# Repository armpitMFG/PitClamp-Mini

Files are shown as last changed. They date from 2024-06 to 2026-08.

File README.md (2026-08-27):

# PitClamp Mini
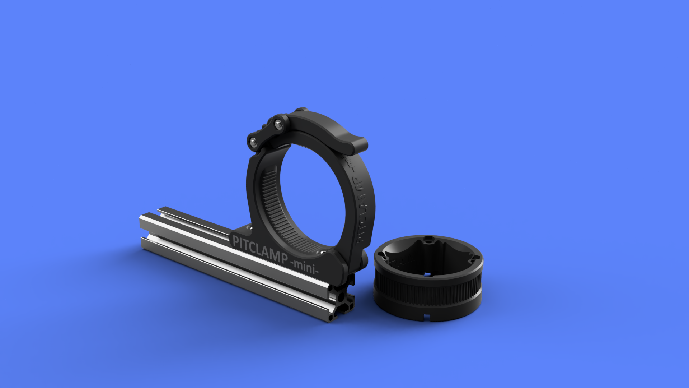
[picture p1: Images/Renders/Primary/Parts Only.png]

## Summary    
3d printed modular quick-release adjustable and removable mount ecosystem for iHSV57, 57AIM, 42AIM, NEMA23 motors. Intended for use with [OSSM](https://www.researchanddesire.com/open-source-sex-machine). 4040/3030 extrusion, flat mount, or clamping base.  

Stress tested to 50 ft-lb without grip being compromised. (PLA 5 walls 15% crosshatch infill)  

### Motor Head Support
  - Default OSSM (57AIM and iHSV57 NEMA23)
  - SpockAroundTheClock's Compact Motor Head (42AIM)
  - just_b's Universal Motor Head (57AIM, 42AIM, and iHSV57 NEMA23)  

### [Purchase A Kit From armpitMFG](https://armpitmfg.etsy.com)

### [Print Files And Instructions](/Files/)  

### [Bill Of Materials](BOM.md)  

### [Assembly Guide Videos](ASSEMBLY_GUIDES.md)

### [Demonstration Videos (SFW)](DEMONSTRATION_VIDEOS.md)

### [Updates](UPDATES.md) (Last updated - 11.22.2024)

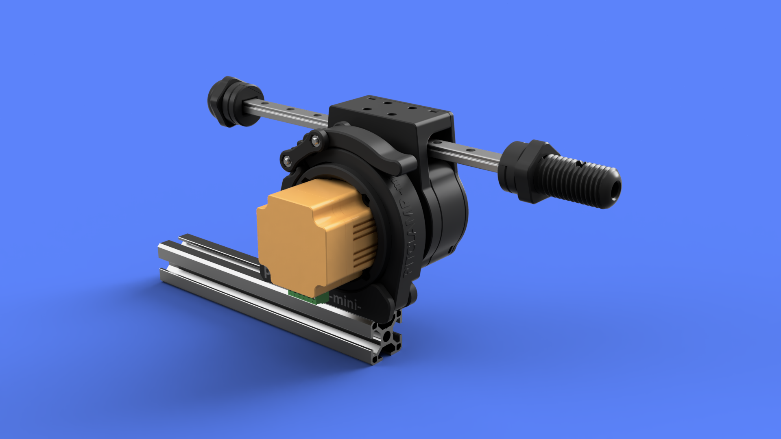
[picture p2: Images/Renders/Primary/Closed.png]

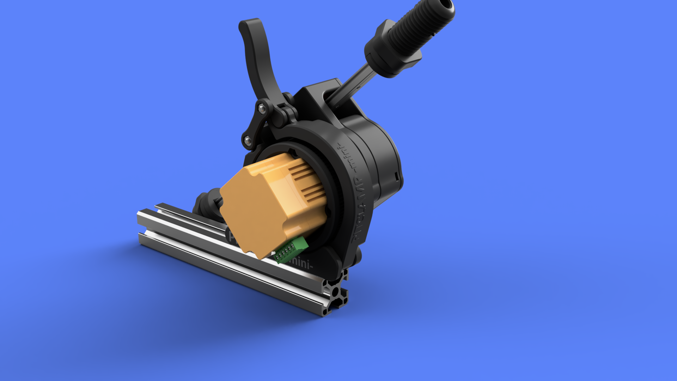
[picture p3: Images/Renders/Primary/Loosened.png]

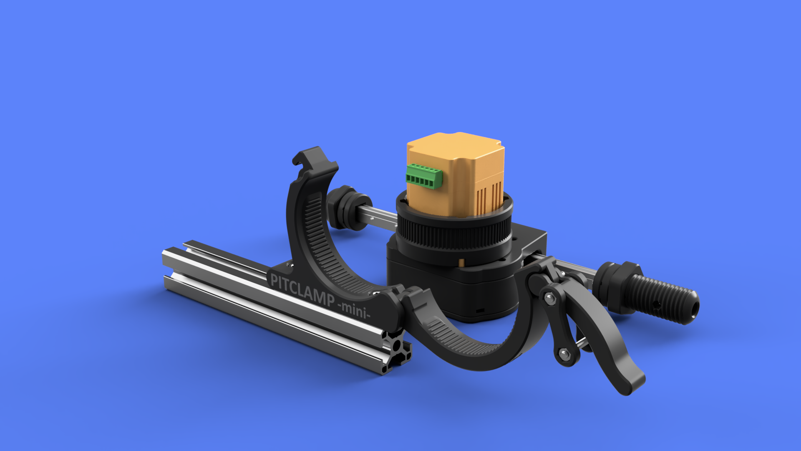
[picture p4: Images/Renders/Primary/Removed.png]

<!-- ![](Images/Renders/View%203/PitClamp%20Mini%20-%2057AIM%20-%20Clamp%20Only.png) -->
<!-- ![](Images/Renders/View%203/PitClamp%20Mini%20-%2057AIM%20-%20Complete.png) -->
<!-- ![](Images/Renders/View%201/PitClamp%20Mini%20-%2057AIM%20-%20Fully%20Open.png) -->
<!-- ![](Images/Renders/View%201/PitClamp%20Mini%20-%2042AIM%20-%20Complete.png) -->

## Features  
  - 4 degree precision quick-adjustable rotation
  - Motor can be quickly removed from mount for storage or use in another base
  - Selection of bases for different use cases
    - Extrusion Top Mount
      - (Extrusion agnostic, but was designed for as small as 3030)
    - Quick Clamp Ratchet + 3030 Extrusion Mount
      - (This mount is the reason behind the whole project)
      - POWERTEC 71408 is the clamp pictured
      - "Guide rail MFT ratchet clamp" search term to find similar prodcuts
    - Double Hinge Folding Mount
       - (Folds flat for easier frame storage, e.g. sliding under bed)
    - (FUTURE) Fully printed Tabletop Clamp
    - (FUTURE) PitClamp-As-Hinges
    - (FUTURE) Pneumatic SC40 Cylinder Pump
  - (FUTURE) Relocatable OSSM Reference Board v2
  - (FUTURE) (Optional) Capacitor located on motor for solder-less pre-v2.3 board compatability  

## Motor Rings

**57AIM - 57AIM15, 57AIM30**  
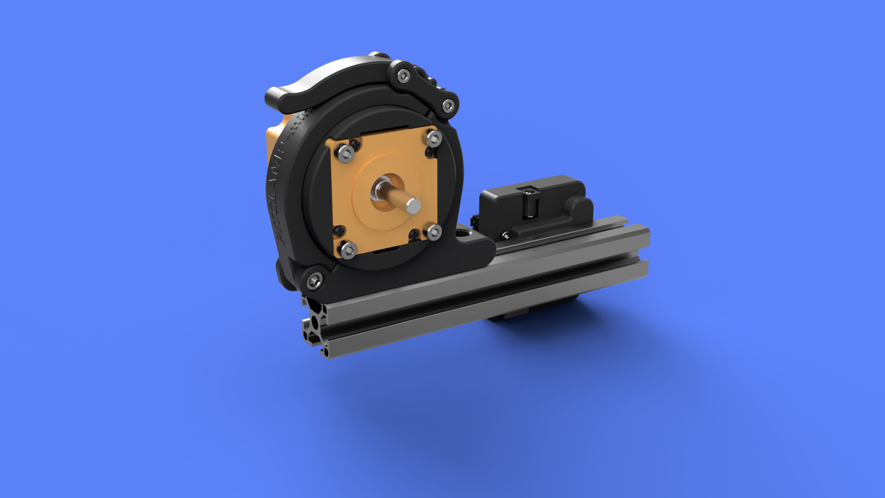
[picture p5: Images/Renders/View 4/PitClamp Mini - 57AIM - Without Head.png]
  
<!-- ![](Images/Renders/View%201/PitClamp%20Mini%20-%2057AIM%20-%20Complete.png)   -->
**iHSV57 -  100w, 140w, 180w**  
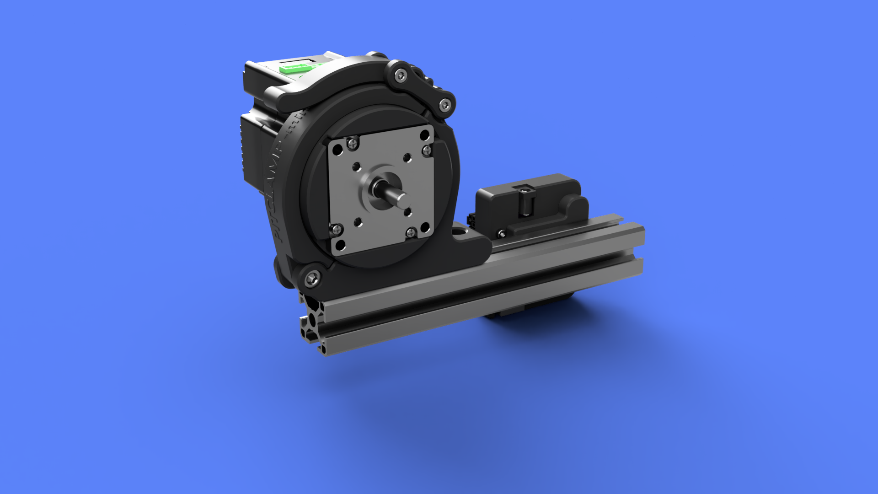
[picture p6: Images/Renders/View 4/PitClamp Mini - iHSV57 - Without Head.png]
  
<!-- ![](Images/Renders/View%201/PitClamp%20Mini%20-%20iHSV57%20-%20Complete.png)   -->
**42AIM - 42AIM15, 42AIM30**
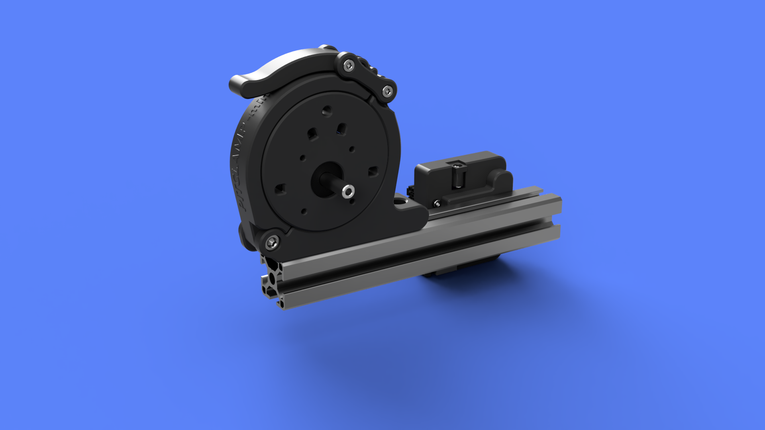
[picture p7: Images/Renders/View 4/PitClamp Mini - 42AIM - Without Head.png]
  
<!-- ![](Images/Renders/View%201/PitClamp%20Mini%20-%2042AIM%20-%20Complete.png)   -->

## Photos
<!-- ![](Images/Photos/PitClamp%20Mini%2057AIM30%204040%20Extrusion.jpg)  
![](Images/Photos/PitClamp%20Mini%2057AIM30%204040%20Extrusion%20Front.jpg)  -->
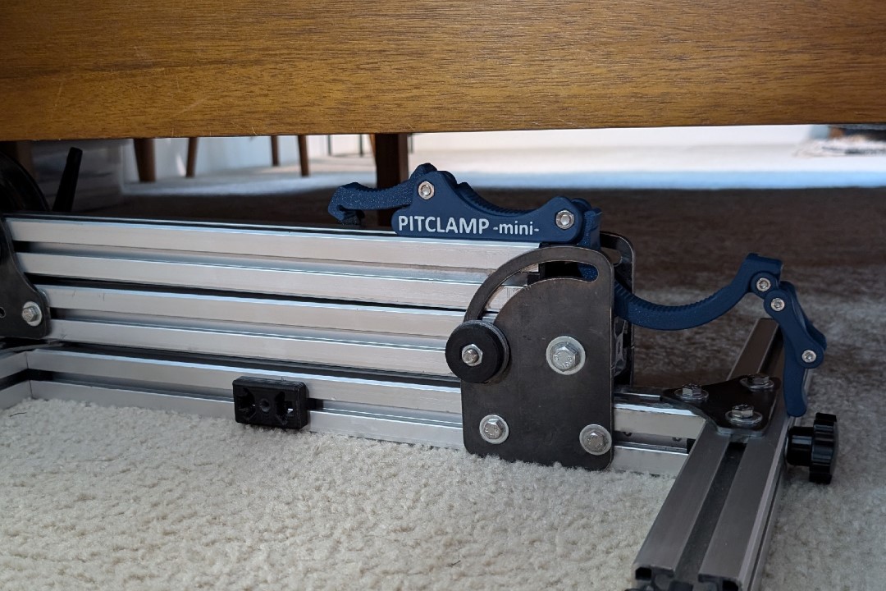
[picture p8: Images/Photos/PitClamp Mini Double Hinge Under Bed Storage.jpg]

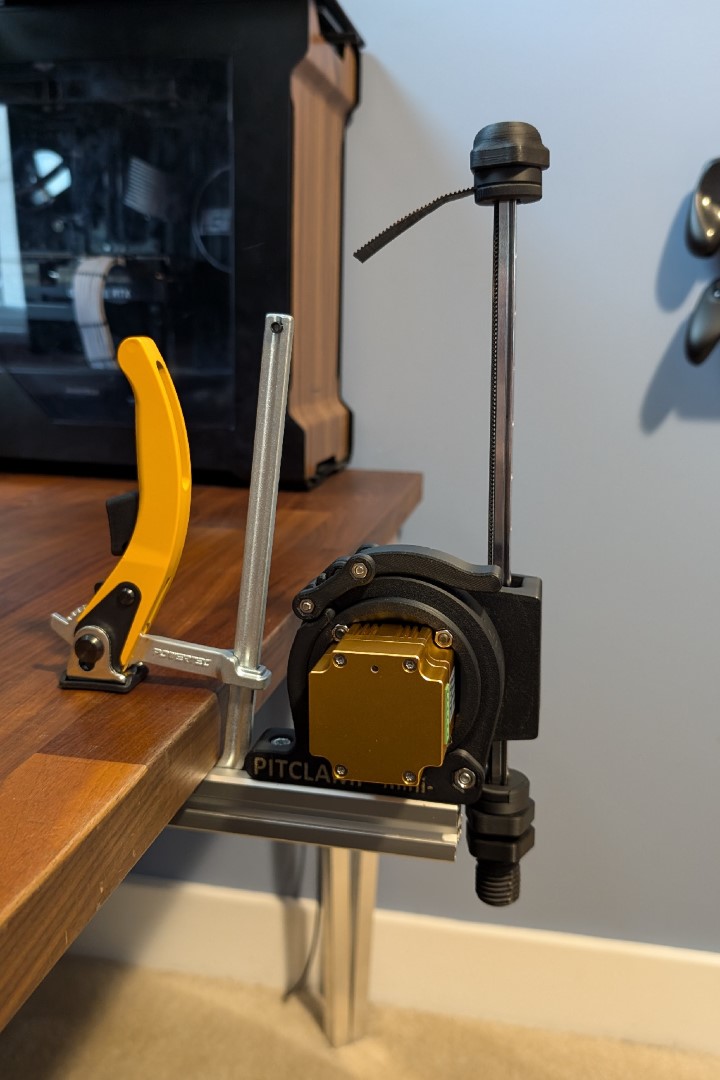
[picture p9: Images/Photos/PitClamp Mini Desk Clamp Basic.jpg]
  
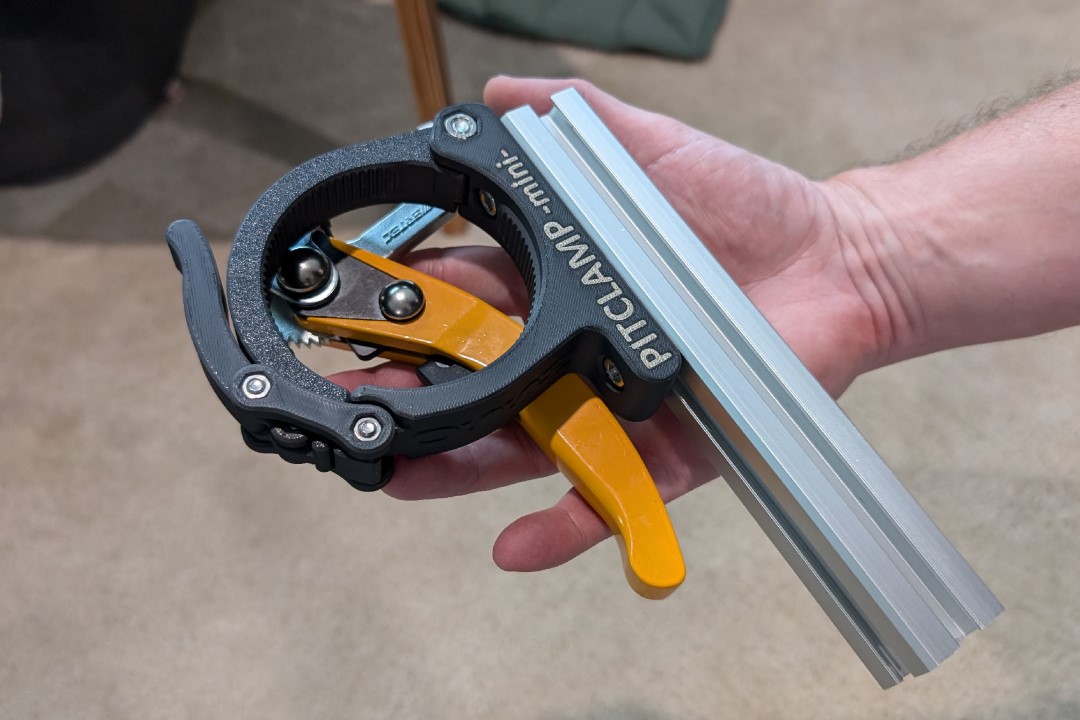
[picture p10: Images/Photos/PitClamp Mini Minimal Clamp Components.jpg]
  
<!-- ![](Images/Photos/PitClamp%20Mini%2057AIM30%203030%20Extrusion%20Modular.jpg) -->
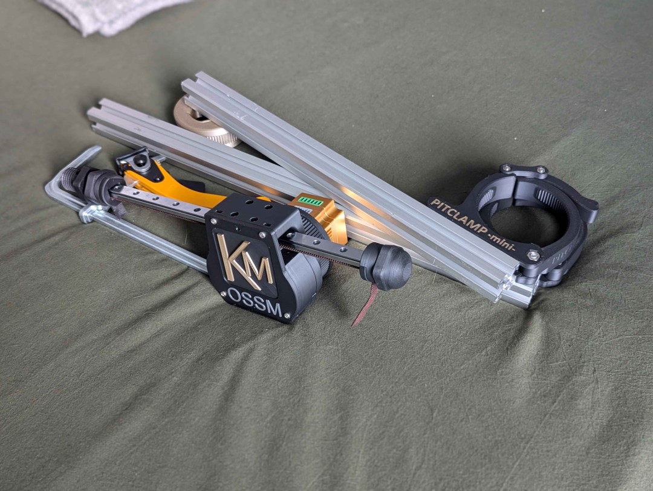
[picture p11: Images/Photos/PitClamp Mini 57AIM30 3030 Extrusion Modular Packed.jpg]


## Roadmap  
**Motor Rings:**
  - 42AIM Motor Ring: 100%  
  - 57AIM Motor Ring: 100%
  - iHSV57 Motor Ring: 100%
  - Extrusion Adapter Ring: 100%

**Clamping Components:**
  - Upper Clamp: 100%  
  - Handle: 100%  
  - Dogbones: 100% 
  - 4040/3030 Extrusion Base: 100%
  - Double Hinge Folding Base: 100%
  - Quick Clamp Tabletop Base: 100%
  - 3d Printed Tabletop Base: 20%
  - (Experimental) Side Mounted PitClamp Mini Hinge Pair: 80%
  - Pneumatic SC40 Cylinder Pump Base: 20%

**Relocatable Reference Board:**
  - Reference Board Case: 75%  
  - Reference Board 4040 Bracket: 90%
  - 42AIM Motor Plug Tidy w/ Capacitor: 75%
  - 57AIM Motor Plug Tidy w/o Capacitor: 0%

**Rail Components:**
  - Screwcap Mini Tensioner: 100%
  - Mini End Effector: 100%
  - XL End Effector: 100%

## Changes from PitClamp v3 
  - Support added for 42AIM motor  
  - Motor ring diameter reduced by 15%  
  - Overall filament required reduced by over 25%  
  - Clamp rotational grip strength increased
  - Motor ring is now reversible in the mount  
  - Clamp "helper" added to reduce adjustment noise/clunkyness  
  - Rear hinge pin is no longer a printed piece
  - Print clarity improved (and optional-default-none) for first and last layer "PitClamp Mini" & "armpitMFG" branding  

## Legacy PitClamp Bases
These bases are being reworked for the PitClamp Mini form factor

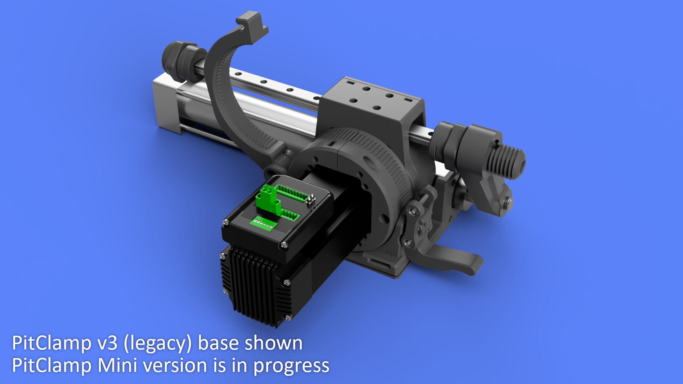
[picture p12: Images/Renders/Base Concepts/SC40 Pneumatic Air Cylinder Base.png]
  
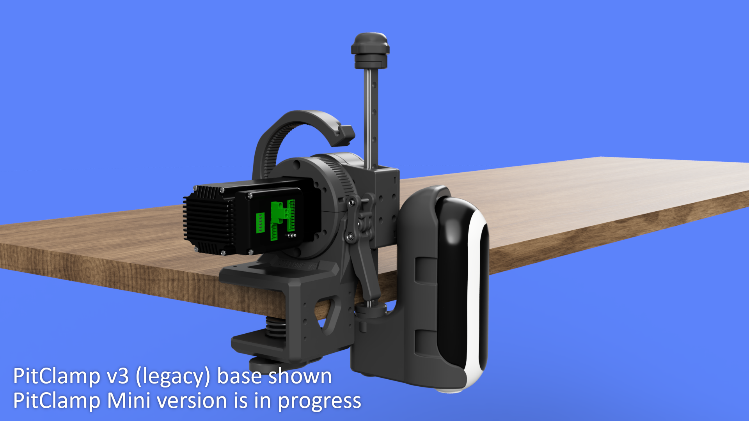
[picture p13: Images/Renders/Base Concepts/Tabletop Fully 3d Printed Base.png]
  

## Licensing

Open-source hardware under the
**[CERN Open Hardware Licence Version 2 - Strongly Reciprocal](LICENSE)**
(`CERN-OHL-S-2.0`), the same licence as the
[OSSM project](https://github.com/KinkyMakers/OSSM-hardware).

Copyright and attribution: [NOTICE.md](NOTICE.md).

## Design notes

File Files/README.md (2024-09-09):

Check out the [Preconfigured 3mf Files](Preconfigured%203mf%20Files/) directory for slicer files that contain all required parts with support and other print settings preconfigured. Just delete the rings that don't apply to your build, select your filament and send the job to your printer. EZ

## Printing:
The entire project is intended for:  
  - 0.4mm nozzle (Wider should not cause problems)
  - 0.2mm layer height (Necessary for some built-in helper features)
  - Standard strength (5 wall) profile
  - 15% gyroid or crosshatch infill
    - Higher infill optional

All parts tested in PLA and PETG  

Supports required for:
  - PitClamp Mini - Common - Handle
  - PitClamp Mini - Base - Standard - Lower
  - PitClamp Mini - Common - Upper
  - PitClamp Mini - Ring - 57AIM
  - PitClamp Mini - Ring - iHSV57

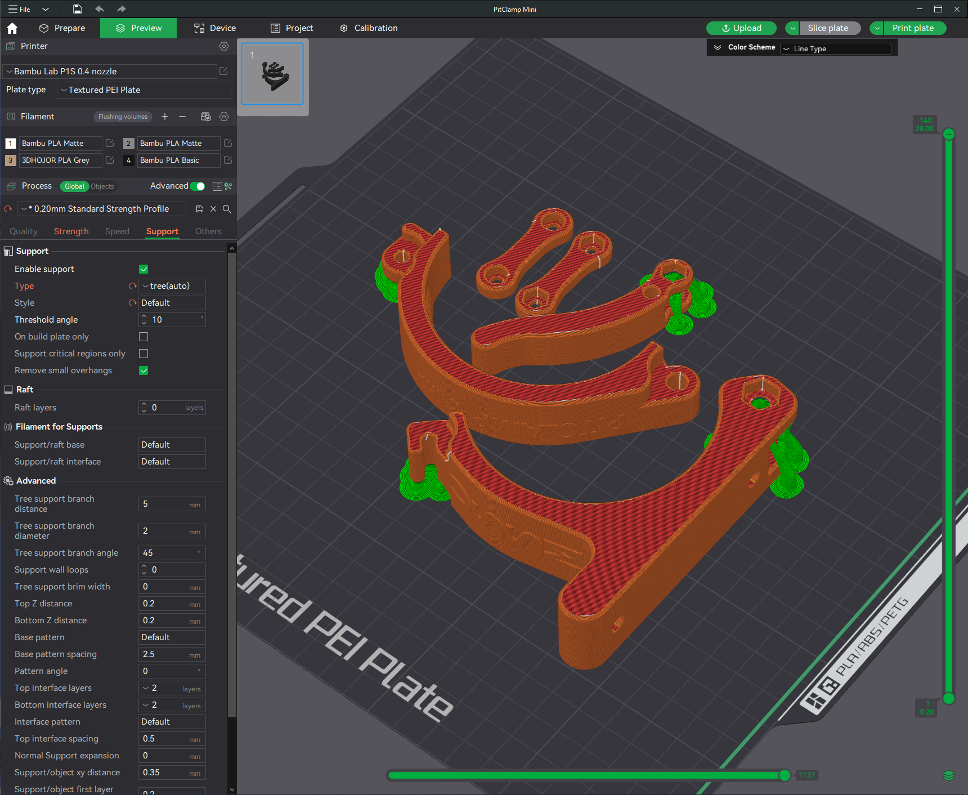
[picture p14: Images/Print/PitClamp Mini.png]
  
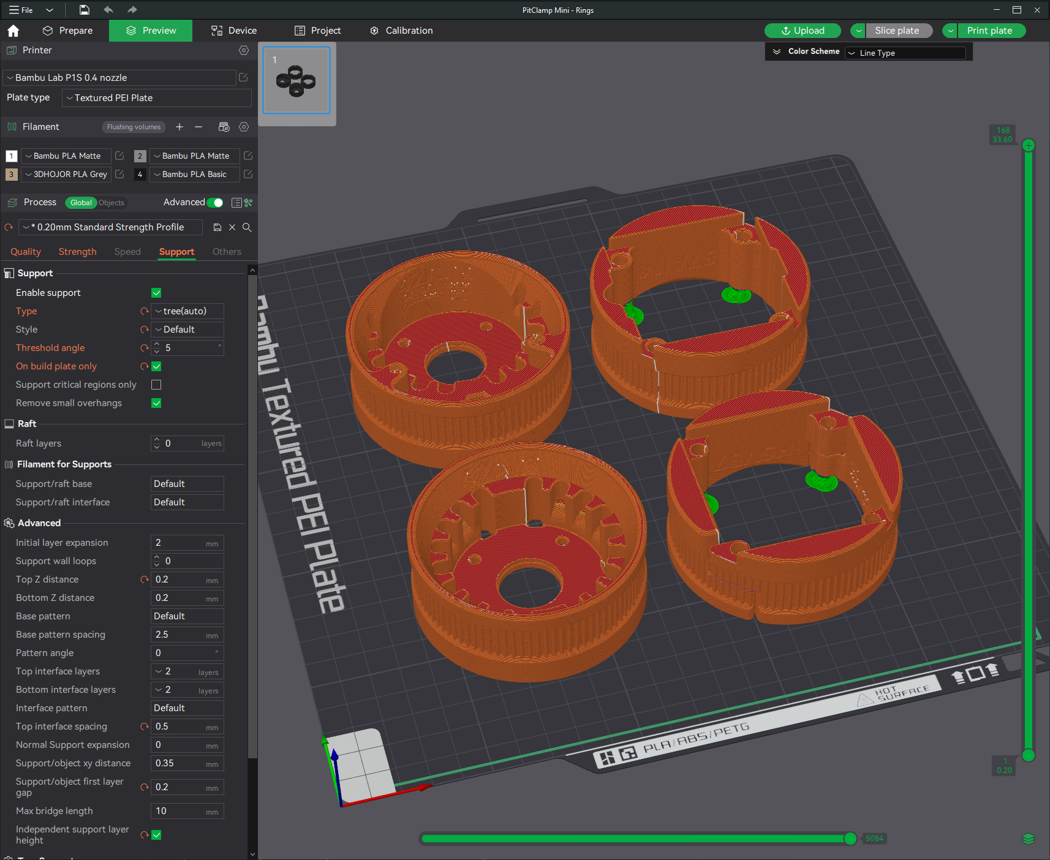
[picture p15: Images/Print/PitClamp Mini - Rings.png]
  

Optional accent color for logo.  
Requires AMS, just paint bucket the flush lettering faces:
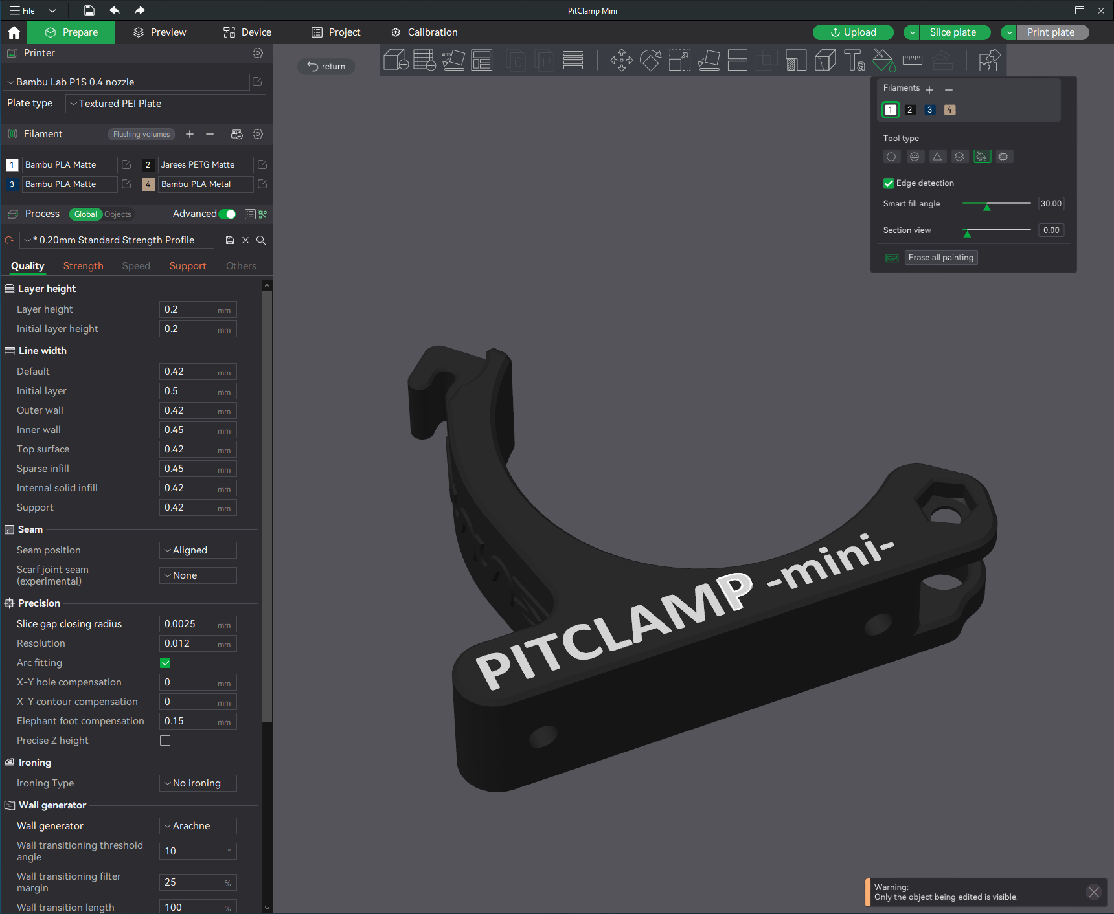
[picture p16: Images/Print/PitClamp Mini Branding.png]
  

## Rings
### Ring Offsets:
- **5mm/6mm offsets** provide clearance for 4040 extrusion. Fine for 3030 setups as well.
    - These are the recommended ring offsets for all setups.
- **0mm/1mm offsets** are designed to sit close to 3030 extrusion. 
    - Only use this offset if you _really_ need things to be compact on 3030 setups. Can have clearance issues if your setup isn't absolutely perfect.

### 42AIM
    For 42AIM motors

### 57AIM
    For 57AIM "Gold" motors

### iHSV57
    For iHSV57 motors.  
    
    This ring is two parts but by using some design trickery it prints as one with minimal supports.  
    
    Ring snaps into two pieces after removing from printer.  
    
    Clasp each half around the motor.

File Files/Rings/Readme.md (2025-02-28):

    //TODO Fill this out better.  

v1.1 Ring (only available for 57AIM) can use M5 nuts or M5 Coupling Nuts (20mm) and has ridges for an interlocking connection to an optional rear motor cover. This is the recommended setup.  
This ring uses 4x M5x35 to attach to the OSSM motor head.

### Pick a ring for your motor based on which actuator head design you are using.  
 - **"Default"** has two diagonal motor mounting bolts recessed an additional 5mm.
    - This is to match the Default OSSM motor head allowing for 4x m5x40mm to be used instead of needing m5x45 for two of them due to the offsets of these mounts in the motor head.
 - **"Alternate"** has all 4 motor mounting bolts recessed the same amount.
    - This is for motor heads such as "Universal motor head" which have matching bolt lengths for assembly.

After testing various designs, the offset has been standardized at +5mm to allow ample clearance for rail tensioners and a sturdier ring.  

Passthru allows for the option of running wires through the ring.  

Most common would be 57AIM - Default, which uses ["PitClamp Mini - Ring v1.1 - 57AIM - 5mm Offset +Passthru.stl"](https://github.com/armpitMFG/PitClamp-Mini/blob/main/Files/Rings/PitClamp%20Mini%20-%20Ring%20v1.1%20-%2057AIM%20-%205mm%20Offset%20%2BPassthru.stl)

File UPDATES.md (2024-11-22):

A stream of updates made to this repo

_Links may go bad, if a reference changes I am not keeping it updated in this file._

- 11.22.2024 - Added v1.1 57AIM Ring (Latest recommended default)
- 09.08.2024 - Refactored file structure.
- 09.08.2024 - Updated to new default files to simplify BOM. 
- 09.04.2024 - Added **Standard Base w/ Helper Brim** STEP file to [Files](/Files/) folder _(Helps prevent latch corner from lifting during print)_
- 09.03.2024 - Added **Ring Template** STEP files to [Ring Template](/Files/Ring%20Template/) folder
- 09.03.2024 - Added **Centered 42AIM Ring** to [Non-Standard Parts](/Files/Non-Standard%20Parts/) folder _(Compatibility with just_b's motor head)_
- 08.29.2024 - Added **57AIM Cable Passthru** Ring to [Non-Standard Parts](/Files/Non-Standard%20Parts/) folder _(Experimenting with motor head mounted Reference Board)_
- 08.28.2024 - Added **[Print-In-Place PitClamp Mini](/Files/Experimental/Print%20In%20Place/)** to [Experimental Parts](/Files/Experimental/) folder _(Reduced hardware)_
- 08.28.2024 - Revised **Extrusion Ring** from Normal to Experimental status _(Needs a stronger design for re-release)_

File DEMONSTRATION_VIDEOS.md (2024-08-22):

##   Modular Mount Demonstration  
[PitClamp Mini - Modular Mount Demonstration  
https://www.youtube.com/watch?v=qSyPyNlI1cM](https://www.youtube.com/watch?v=qSyPyNlI1cM)  

##   Desk Clamp Demonstration
[PitClamp Mini - Desk Clamp Demonstration  
https://www.youtube.com/watch?v=EhhH3YP36sw](https://www.youtube.com/watch?v=EhhH3YP36sw)  

##   Torque test to failure (OSSM Head Failure)
[PitClamp Mini - Torque test to failure  
https://www.youtube.com/watch?v=X3qTg1i2Ts0](https://www.youtube.com/watch?v=X3qTg1i2Ts0)

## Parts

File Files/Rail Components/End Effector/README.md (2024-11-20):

## Multipurpose End Effector Tensioner

Inspired by Jack's 24mm effector + tensioner  
Inspired by JRG's clampring tidy-up

**Notes**  
Multipurpose_End_Effector_Tensioner_Medium is the end I would recommend.   
Multipurpose_End_Effector_Tensioner_Short will give you 25mm additional travel but should be reserved for non-heavy-duty applications  

**Summary**  
//TODO

**Hardware**  
2x m3x16 + nuts

**Printing**  
Use a 2 layer raft under the threads for better adhesion  
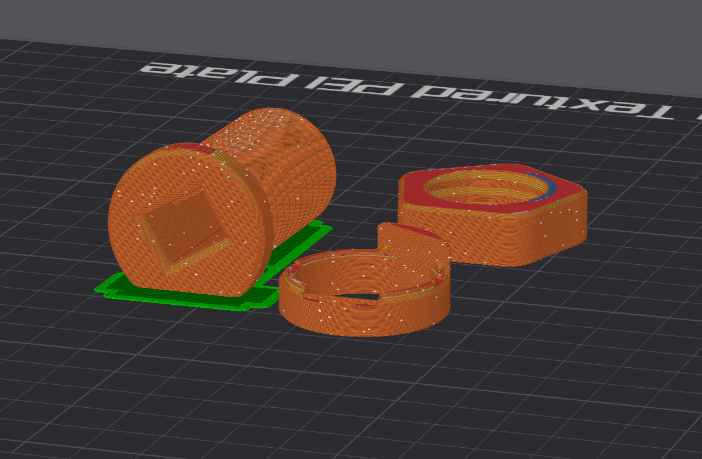
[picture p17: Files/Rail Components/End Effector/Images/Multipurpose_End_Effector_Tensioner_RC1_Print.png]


**Assembly**  
//TODO

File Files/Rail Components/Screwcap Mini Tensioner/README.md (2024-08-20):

## Screwcap Mini Tensioner
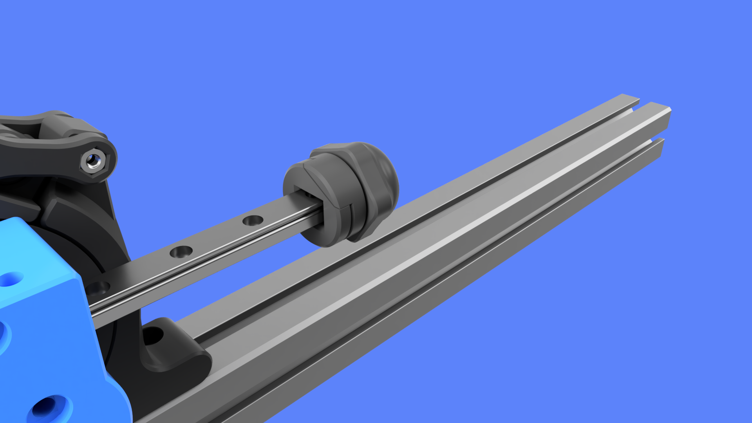
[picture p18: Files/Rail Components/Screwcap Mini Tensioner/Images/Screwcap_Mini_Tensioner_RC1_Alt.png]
Cover Photo


**Summary**  
This is a compact belt tensioner that supports up to 12mm belts.  
Smooth-styling, no exposed hardware. Safer for accidental contact.  

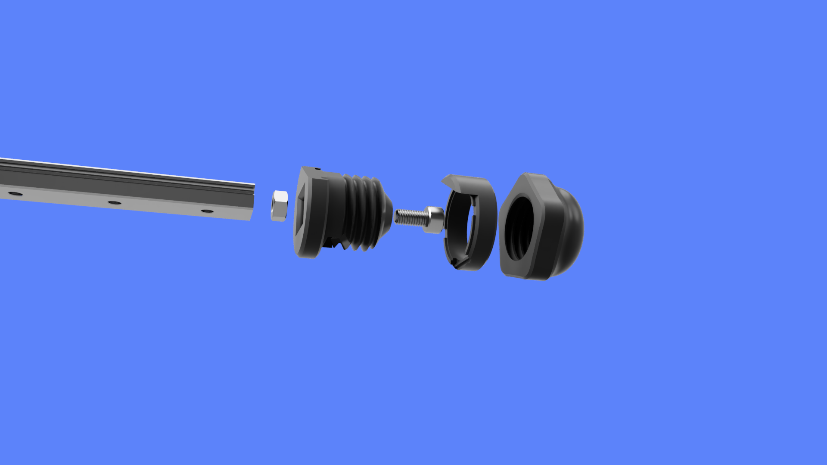
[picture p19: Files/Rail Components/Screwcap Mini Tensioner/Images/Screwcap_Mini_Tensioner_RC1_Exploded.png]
Exploded view

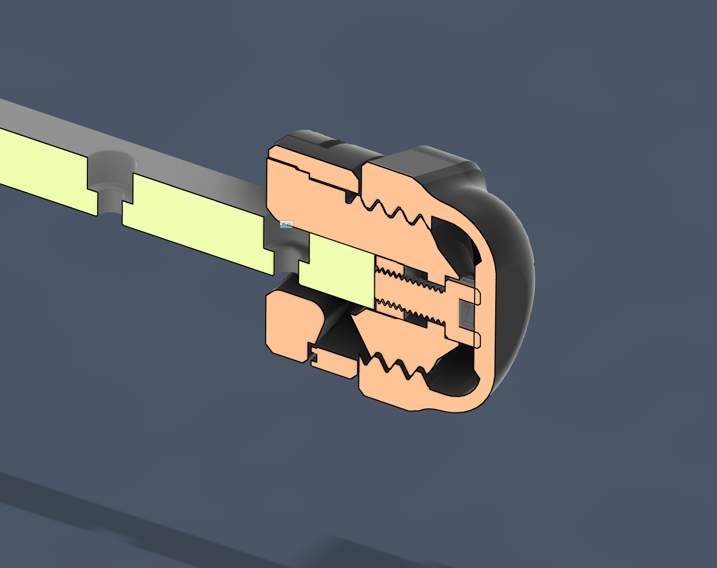
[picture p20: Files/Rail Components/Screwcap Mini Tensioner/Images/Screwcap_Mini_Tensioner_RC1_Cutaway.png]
Cutaway view


**Hardware**  
M5x10 Socket Cap Head Bolt  
M5 Nut

**Printing**  
Recommended profile: Strength, 20% infill

Screwcap_Mini_Tensioner_Ring - No supports  
Screwcap_Mini_Tensioner_Cap - Supports necessary, just needs to hold up the middle  
Screwcap_Mini_Tensioner_Base - Print on a small raft, I used 2 layer raft

For best results, print using "Variable layer height" for Screwcap_Mini_Tensioner_Base and Screwcap_Mini_Tensioner_Cap. It's really worth the extra time here.

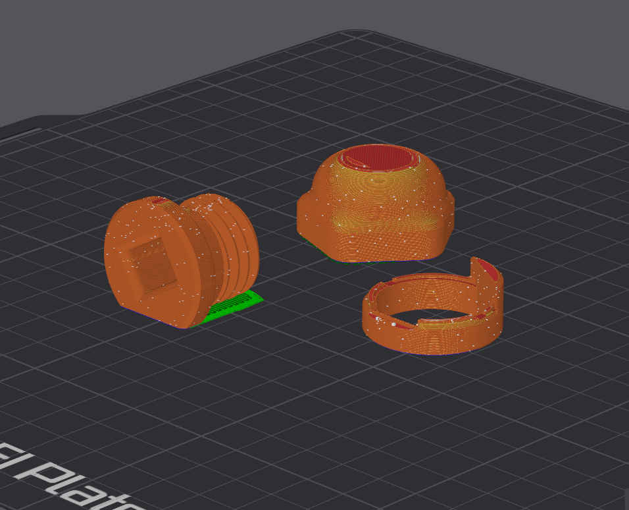
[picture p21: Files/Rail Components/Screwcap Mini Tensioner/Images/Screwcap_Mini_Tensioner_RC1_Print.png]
Print view


##   Screwcap Mini Tensioner Installation

[Screwcap Mini Tensioner Installation  
https://www.youtube.com/watch?v=DaN17W8FflY](https://www.youtube.com/watch?v=DaN17W8FflY)
 
**Assembly**  

Drop nut into the Base. Screw in the bolt lightly from the other side until the nut is secured into the base of the hole.  
Loosen the bolt unil there is small gap visible between it and the Base  
Slide belt through Base opening, slide base onto rail  
Pull tension on the belt while sliding the Ring into place  
While keeping tension on the belt, screw on the cap.

You should feel the cap hit the head of the screw, and as you tighten from there it will move the tensioner away from the rail while also tightening it's grip on the belt. Unscrew and adjust the bolt position and repeat the process if you need to vary the tension.

**Attributions**  
Inspired by Jack's 24mm effector + tensioner  
Inspired by JRG's clampring tidy-up

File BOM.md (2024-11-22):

# PitClamp Mini Bill Of Materials 

## Motor Rings:

### 57AIM 
Default Motor Head, use Default (v1.1 ring)  
Alternate Head, use Alternate

    v1.1 ring - can use 4x M5x35 Socket Cap Head Bolt (Default that are included with R+D OSSM parts kit)
    Other rings - use 4x M5x40 Socket Cap Head Bolt
    4x M5 Nuts

### iHSV57
Default Motor Head, use Default  
Alternate Head, use Alternate

      4x M5x40 Socket Cap Head Bolt
      4x M5 Nuts

### 42AIM
SpockAroundTheClock's Compact Motor Head, use SATC  
just_b's Universal Motor Head, use Centered  

      1x M5x50 Socket Cap Head Bolt
      1x M5 Nut
      4x M3x16 Socket Cap Head Bolt

## Latching Mechanism:
    2x M4x25 Socket Cap Head Bolt
    1x M4x12 or M4x10 Socket Cap Head Bolt
    3x M4 Nut

## Bases:

###  Standard Base
    Rear Hinge:
      1x M6x20 Socket Cap Head Bolt
      1x M6 Nut
    Attaching Base to Extrusion:
      2x M6x20 (M6x15 for 3030 Extrusion) Socket Cap Head Bolt
      2x M6 T-Nut

###  Double Hinge Base
    Rear Hinge:
      1x M6x20 Socket Cap Head Bolt
      1x M6 Nut
    Front Hinge:
      1x M6x20 Socket Cap Head Bolt
      1x M6 Nut
    For attaching Base to Extrusion:
      2x M6x20 (M6x15 for 3030 Extrusion) Socket Cap Head Bolt
      2x M6 T-Nut

<!-- ### (FUTURE, maybe) Side Mount Base
    For attaching to 3030 extrusion:
      2x M6x20 Socket Cap Head Bolt //TODO: Confirm that M6x25 is too long
      2x M6 T-Nut
    For attaching to 4040 extrusion:
      2x M6x25 Socket Cap Head Bolt
      2x M6 T-Nut -->

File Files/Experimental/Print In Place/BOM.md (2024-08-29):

# PitClamp Mini Print In Place Bill Of Materials 

## Latching Mechanism:
    2x M4x25 Socket Cap Head Bolt
    2x M4 Nut

## Bases:
    Attaching Base to Extrusion:
      2x M6x20 (M6x15 for 3030 Extrusion) Socket Cap Head Bolt
      2x M6 T-Nut

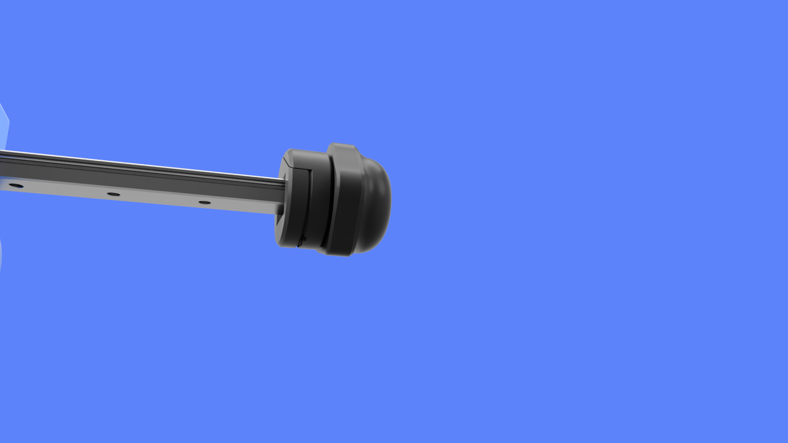
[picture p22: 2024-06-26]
Files/Rail Components/Screwcap Mini Tensioner/Images/Screwcap_Mini_Tensioner_RC1.png

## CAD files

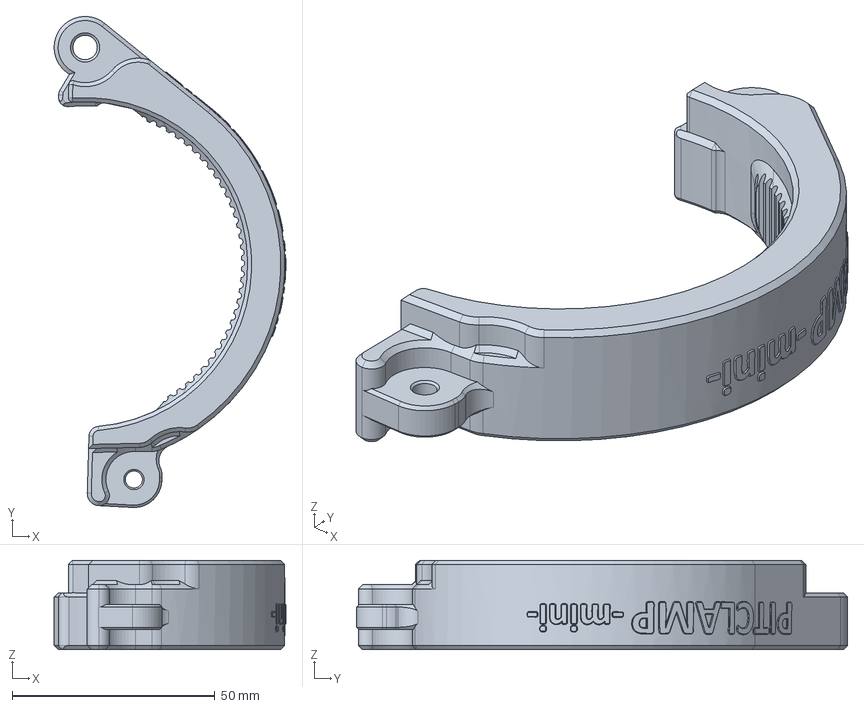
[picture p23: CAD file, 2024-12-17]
Files/Bases/STEP/PitClamp Mini - Common - Upper.step
57.2 x 121.1 x 22.0 mm

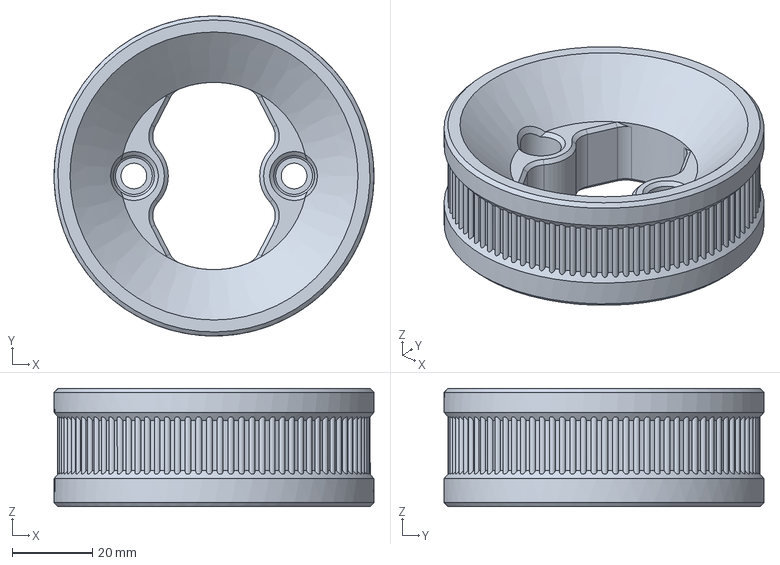
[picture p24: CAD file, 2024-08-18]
Files/Experimental/Extrusion Ring/STEP/PitClamp Mini - Ring - Extrusion - 1mm Offset.step
79.9 x 79.9 x 29.6 mm

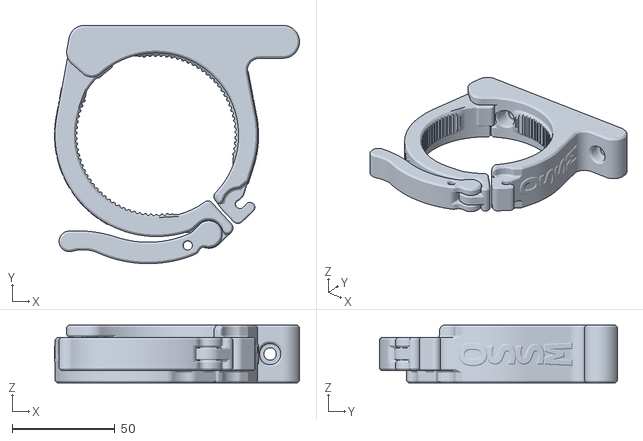
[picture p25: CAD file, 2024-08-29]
Files/Experimental/Print In Place/PitClamp Mini - Standard - Print-In-Place.stl
119.0 x 115.7 x 28.0

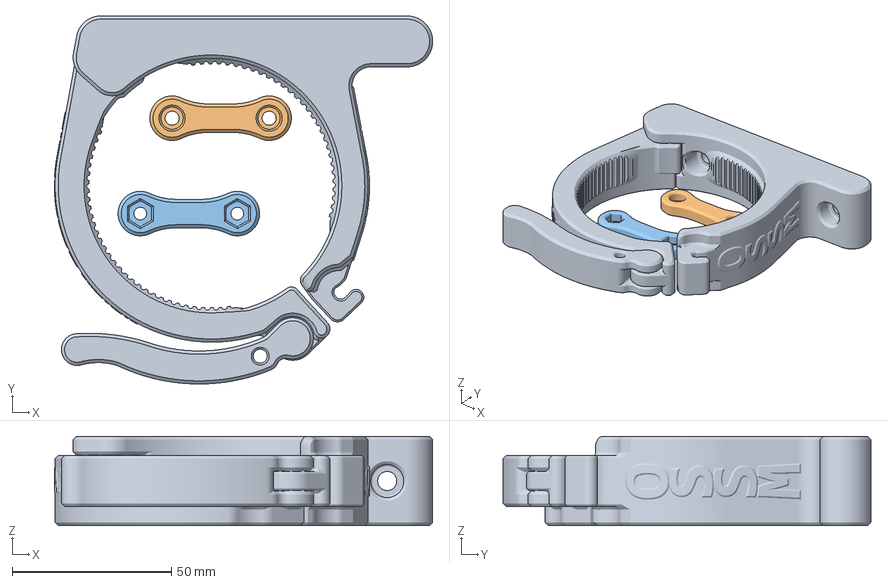
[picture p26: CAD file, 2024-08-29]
Files/Experimental/Print In Place/Preconfigured 3mf Files/PitClamp Mini - Standard - Print-In-Place.3mf
119.0 x 115.7 x 28.0 mm
PitClamp Mini - Standard - Print-In-Place.step
PitClamp Mini - Common - Dogbone Bolts.step
PitClamp Mini - Common - Dogbone Nuts.step

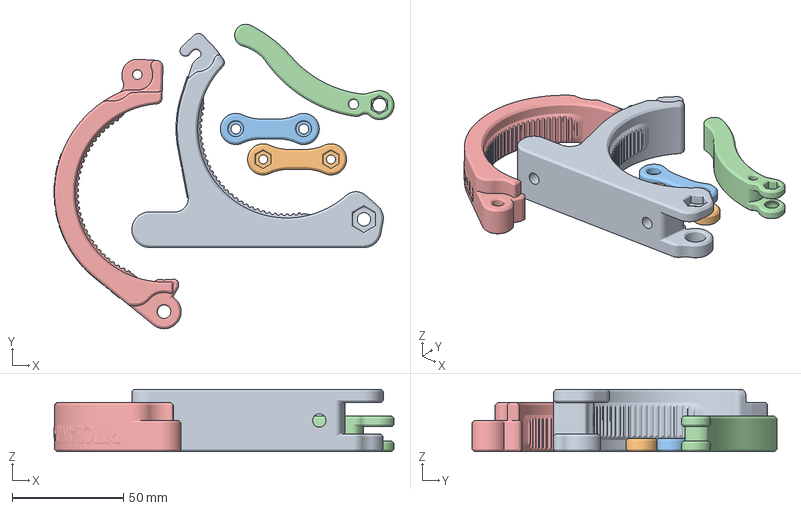
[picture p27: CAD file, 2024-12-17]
Files/Preconfigured 3mf Files/PitClamp Mini.3mf
152.9 x 136.9 x 28.0 mm
PitClamp Mini - Base - Standard.step
PitClamp Mini - Common - Dogbone Nuts.step
PitClamp Mini - Common - Dogbone Bolts.step
PitClamp Mini - Common - Handle.step
PitClamp Mini - Common - Upper.step

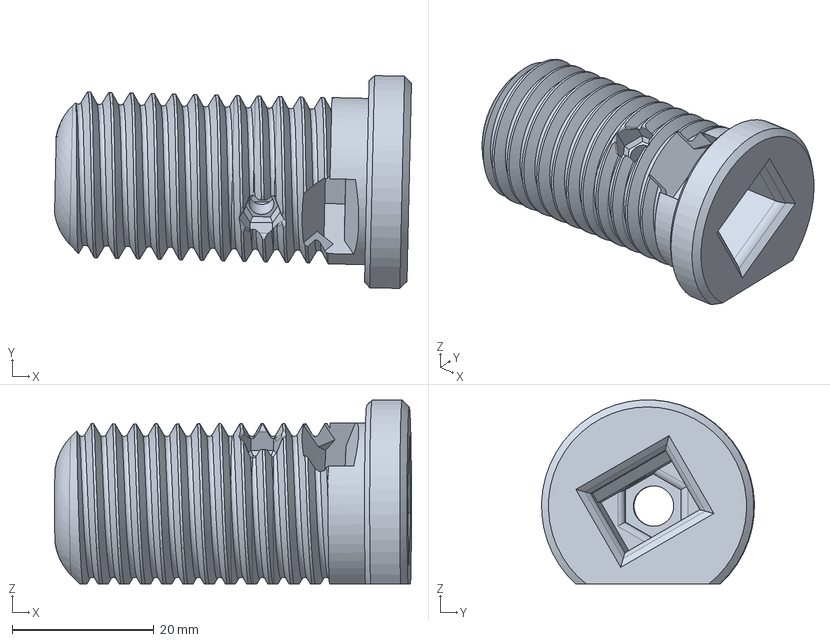
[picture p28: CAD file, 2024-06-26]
Files/Rail Components/End Effector/Files/STEP/Multipurpose_End_Effector_Tensioner_Short_RC1.step
50.4 x 30.1 x 26.0 mm

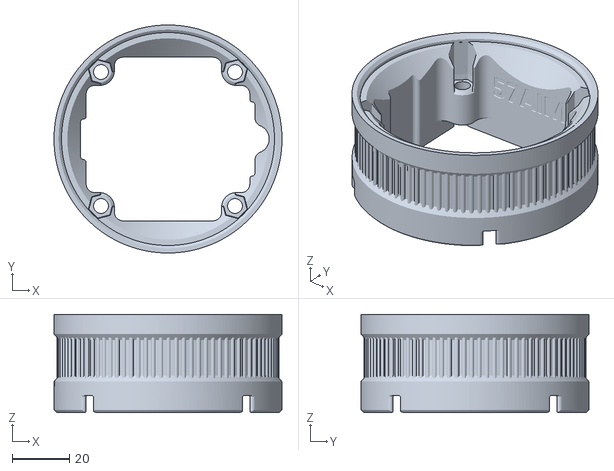
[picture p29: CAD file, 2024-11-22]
Files/Rings/PitClamp Mini - Ring v1.1 - 57AIM - 5mm Offset +Passthru.stl
80.0 x 80.0 x 34.5

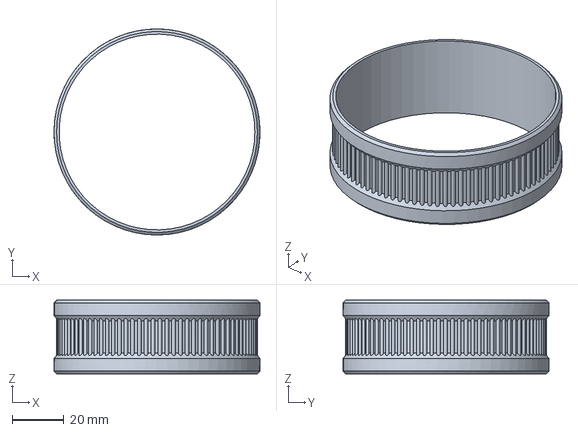
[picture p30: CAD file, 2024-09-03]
Files/Rings/Ring Template/Ring Template - 0mm Offset.step
79.9 x 79.9 x 28.6 mm

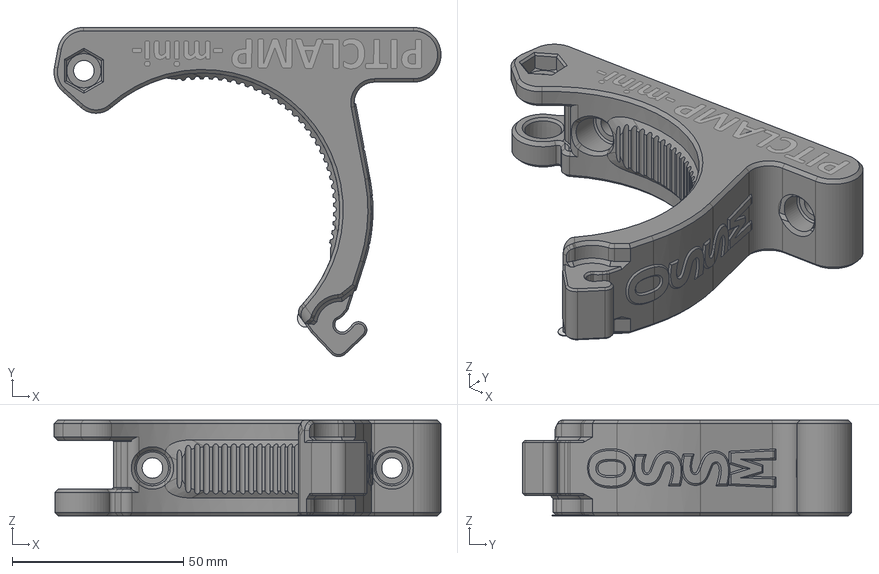
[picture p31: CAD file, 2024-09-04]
Files/Bases/STEP/PitClamp Mini - Base - Standard - Lower - With Helper Brim.step
113.1 x 96.2 x 28.0 mm

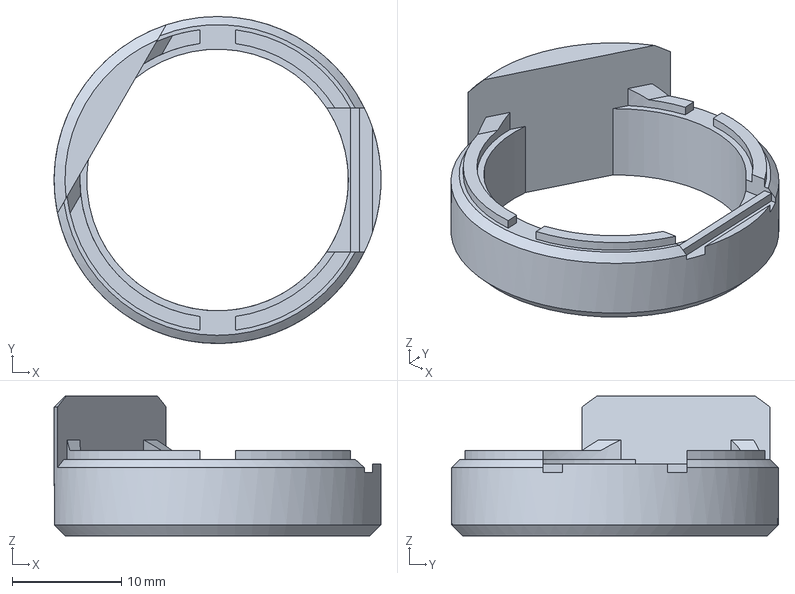
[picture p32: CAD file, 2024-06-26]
Files/Rail Components/End Effector/Files/STEP/Multipurpose_End_Effector_Tensioner_Ring_RC1.step
30.0 x 30.0 x 12.8 mm

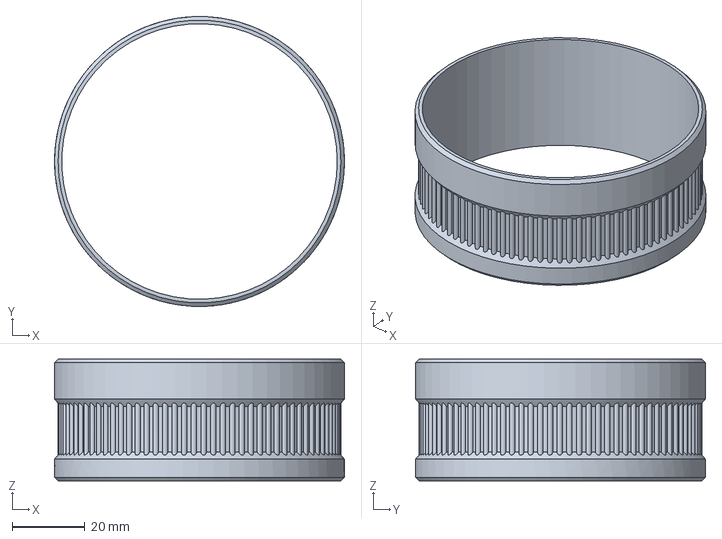
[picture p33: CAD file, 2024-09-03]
Files/Rings/Ring Template/Ring Template - 5mm Offset.step
79.9 x 79.9 x 33.6 mm

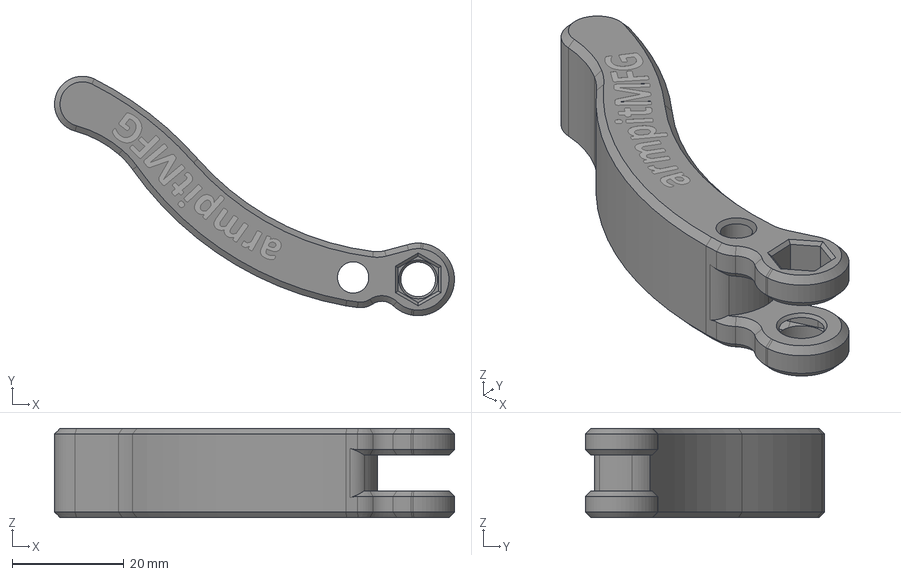
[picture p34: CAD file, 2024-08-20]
Files/Bases/STEP/PitClamp Mini - Common - Handle.step
71.6 x 42.9 x 16.0 mm

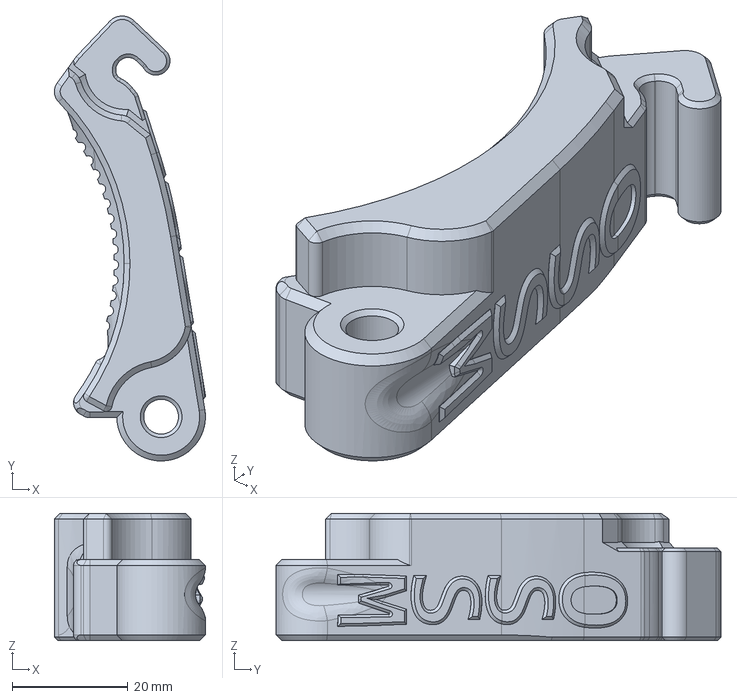
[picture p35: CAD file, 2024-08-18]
Files/Bases/STEP/PitClamp Mini - Base - Folding - Rear.step
26.1 x 76.8 x 22.0 mm

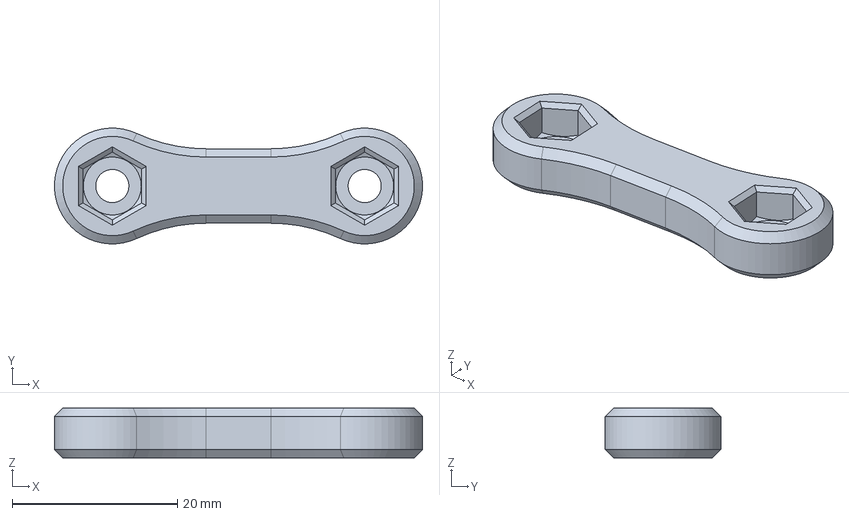
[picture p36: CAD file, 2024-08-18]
Files/Bases/STEP/PitClamp Mini - Common - Dogbone Nuts.step
44.5 x 14.0 x 6.00 mm

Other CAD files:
Files/Experimental/Extrusion Ring/STEP/PitClamp Mini - Ring - Extrusion - 6mm Offset.step
Files/Bases/STEP/PitClamp Mini - Base - Folding - Lower.step
Files/Bases/STEP/PitClamp Mini - Base - Standard - Lower.step
Files/Rail Components/Screwcap Mini Tensioner/Files/Screwcap_Mini_Tensioner_RC1.3mf
Files/Bases/PitClamp Mini - Base - Folding - Lower.stl
Files/Bases/PitClamp Mini - Base - Folding - Rear.stl
Files/Bases/PitClamp Mini - Base - Standard - Lower.stl
Files/Bases/PitClamp Mini - Common - Dogbone Bolts.stl
Files/Bases/PitClamp Mini - Common - Dogbone Nuts.stl
Files/Bases/PitClamp Mini - Common - Handle.stl
Files/Bases/PitClamp Mini - Common - Upper.stl
Files/Bases/STEP/PitClamp Mini - Common - Dogbone Bolts.step
Files/Experimental/Extrusion Ring/PitClamp Mini - Ring - Extrusion - 1mm Offset.stl
Files/Experimental/Extrusion Ring/PitClamp Mini - Ring - Extrusion - 6mm Offset.stl
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

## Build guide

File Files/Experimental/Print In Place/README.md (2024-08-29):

# PitClamp Mini (Print-In-Place)

### [Bill Of Materials](BOM.md)  
### [Preconfigured 3mf Files](Preconfigured%203mf%20Files/) has slicer file that contains support and other print settings preconfigured.

## Summary    
This is the same as PitClamp Mini, but reduces hardware requirements by replacing the rear hinge (M6x20) and Handle Lever hinge (M4x12) with hinges that are printed in place.  

The clearance used in the hinge gaps is 0.15mm, you should have your printer dialed in before trying this print.   

The hinges should break loose after printing without much difficulty.   

## Other Parts:
You will also need (from the main file directory):

    PitClamp Mini - Common - Dogbone Bolts
    PitClamp Mini - Common - Dogbone Nuts
    Ring of your choice

## Printing:
The entire project is intended for:  
  - 0.4mm nozzle (Wider should not cause problems)
  - 0.2mm layer height (Necessary for some built-in helper features)
  - Standard strength (5 wall) profile
  - 15% gyroid or crosshatch infill
    - Higher infill optional

Print in the provided STL orientation

### Supports
Required under the handle and by the hinge.  
I used organic/tree supports, set to 10 degree threshold. 

Recommended supports are all visible in this image:
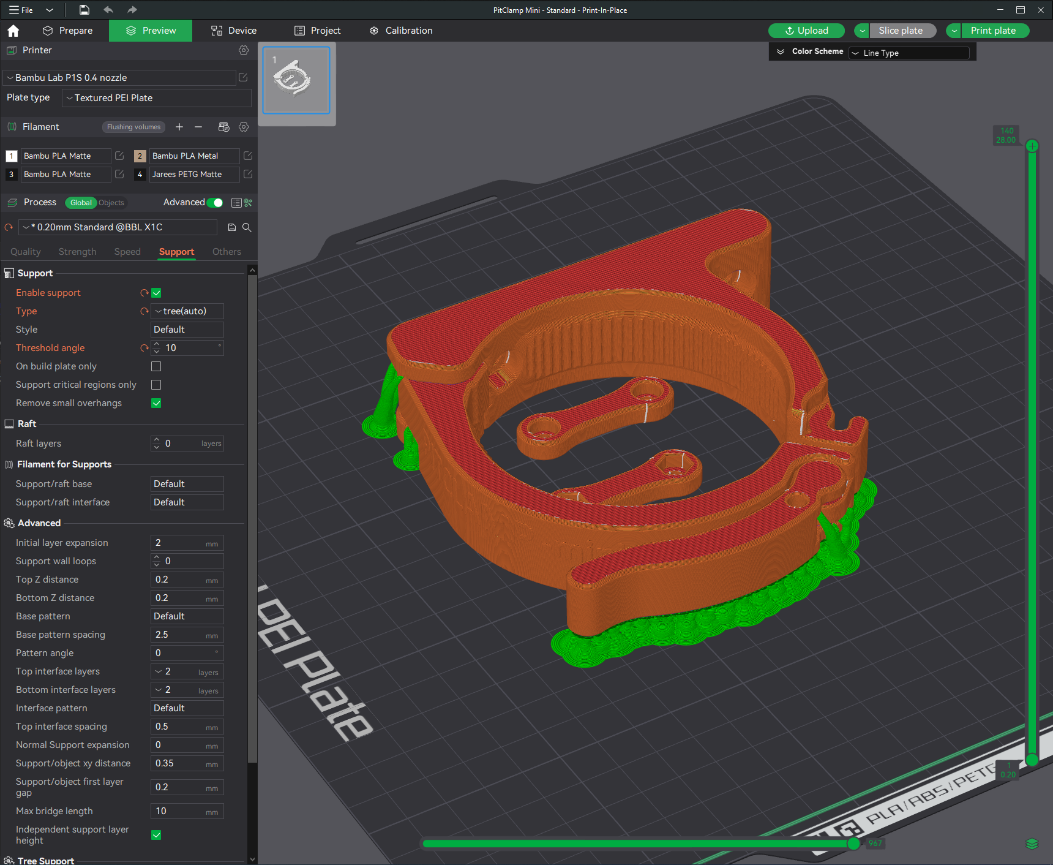
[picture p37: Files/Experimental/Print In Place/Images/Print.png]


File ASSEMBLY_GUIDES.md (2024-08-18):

##   PitClamp Mini - Body Assembly  
[PitClamp Mini - Body Assembly  
https://www.youtube.com/watch?v=61Ln6gqgMoM](https://www.youtube.com/watch?v=61Ln6gqgMoM)  

##   PitClamp Mini - Ring 57AIM Installation 
[PitClamp Mini - Ring 57AIM Installation  
https://www.youtube.com/watch?v=yFO8ejC_tYA](https://www.youtube.com/watch?v=yFO8ejC_tYA)

##   PitClamp Mini - Ring iHSV57 print post processing
[PitClamp Mini - Ring iHSV57 print post processing  
https://www.youtube.com/watch?v=xeE-M1KEnYc](https://www.youtube.com/watch?v=xeE-M1KEnYc)

##   Screwcap Mini Tensioner Installation
[Screwcap Mini Tensioner Installation  
https://www.youtube.com/watch?v=DaN17W8FflY](https://www.youtube.com/watch?v=DaN17W8FflY)

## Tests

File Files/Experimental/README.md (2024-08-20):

This directory is for experimental parts.  

These parts should only be used if you know what you're doing, they may cause your PitClamp Mini setup to be less than optimal, and it's possible they have never even been print tested.

    //TODO: Fill this out a little better.

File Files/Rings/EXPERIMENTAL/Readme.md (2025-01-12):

This directory is for experimental parts.  

These parts should only be used if you know what you're doing, they may cause your PitClamp Mini setup to be less than optimal, and it's possible they have never even been print tested.

    //TODO: Fill this out a little better.

## 60AIM40F Motor Ring
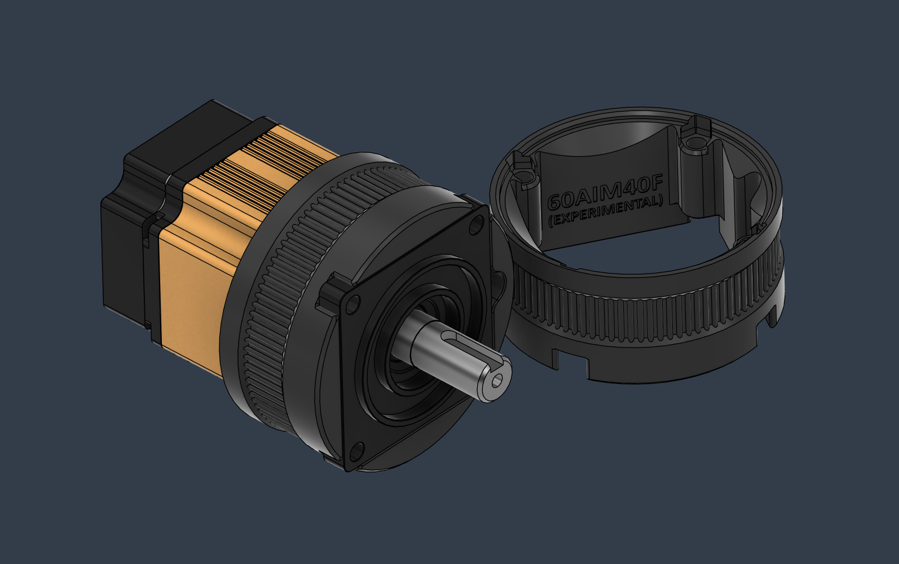
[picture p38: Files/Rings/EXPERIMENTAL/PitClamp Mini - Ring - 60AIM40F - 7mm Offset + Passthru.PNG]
Example

Print tested and motor fit confirmed.

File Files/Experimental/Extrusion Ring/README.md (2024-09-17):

# (EXPERIMENTAL) Extrusion Ring

## Summary
Connects to 3030/4040 extrusion to then use in a PitClamp Mini.  
This allows you to make a quick-disconnect motor arm that attaches to any other base.

Intended to be used with Quick Clamp Ratchet base, but be creative!

**Reason for "Experimental" tag:**  
There are known structural weaknesses in this part, they must be addressed.  
Recommended only for lighter use cases at this time.

## BOM
For attaching to 3030 extrusion:  
1mm offset

      2x M6x20 Socket Cap Head Bolt //TODO: Confirm that M6x25 is too long
      2x M6 T-Nut

For attaching to 4040 extrusion:  
6mm offset

      2x M6x25 Socket Cap Head Bolt
      2x M6 T-Nut

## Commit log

2024-06-26 Add select initial BETA files
    Images and multipurpose end effector tensioner
    [Jam Nut.step, Jam Nut.stl, Multipurpose End Effector Tensioner Ring.step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]
2024-06-26 BETA partial file release
    [Jam Nut.step, Jam Nut.stl, Multipurpose End Effector Tensioner Ring_RC1.step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]
2024-06-26 Landing page readme with images
2024-06-30 Add motor ring images
2024-07-27 Refactor file paths for consistency
    [Jam Nut.step, Jam Nut.stl, Multipurpose End Effector Tensioner Ring_RC1.step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]
2024-07-27 More renaming for consistency
    [Jam_Nut.stl, Multipurpose_End_Effector_Tensioner_Ring_RC1.stl]
2024-08-15 Fixing strange angle that was applied to objects
    [Screwcap_Mini_Tensioner_RC1.3mf]
2024-08-15 Add medium length end effector tensioner (Default)
2024-08-15 Add 3mf for complete tensioner and end effector (Default)
2024-08-15 Revision to end effector Medium (proper rail fit, reduced complexity)
2024-08-15 File renaming/cleanup for consistency
    [Jam_Nut.step, Multipurpose_End_Effector_Tensioner_Ring_RC1.step, Multipurpose_End_Effector_Tensioner_Short_RC1.step]
2024-08-17 v1.0 Bill Of Materials
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2024-08-18 PitClamp Mini v1.0 Release
    [Jam Nut.step, Jam_Nut.step, Jam_Nut.stl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]
2024-08-18 Remove duplicate files
    [Multipurpose End Effector Tensioner Ring_RC1.step, Multipurpose End Effector Tensioner Short_RC1.step]
2024-08-18 Add demonstration images for Quick Clamp Tabletop
2024-08-20 Add ULTRA-EXPERIMENTAL folder and printed hinge pin
    [PitClamp Mini - Printed Hinge - Clip.step, PitClamp Mini - Printed Hinge - Nut.step, PitClamp Mini - Printed Hinge - Pin.step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]
2024-08-20 Add unbranded standard base (by request)
    [PitClamp Mini - Base - Standard (Unbranded).step, PitClamp Mini - Base - Standard (Unbranded).stl]
2024-08-20 Move "Experimental" tag from Extrusion Ring, passes tests
    [PitClamp Mini - Ring - Extrusion - 1mm Offset.stl, PitClamp Mini - Ring - Extrusion - 6mm Offset.stl]
2024-08-20 Printed Hinge Pin
    [PitClamp Mini - Printed Hinge - Clip.step, PitClamp Mini - Printed Hinge - Nut.step, PitClamp Mini - Printed Hinge - Pin.step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]
2024-08-20 Bring Extrusion Rings into Standard Release
    [PitClamp Mini - Ring - Extrusion - 1mm Offset.step, PitClamp Mini - Ring - Extrusion - 1mm Offset.stl, PitClamp Mini - Ring - Extrusion - 6mm Offset.step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]
2024-08-20 Widen Handle nut opening by 0.1mm
    [PitClamp Mini - Common - Handle.step, PitClamp Mini - Common - Handle.stl, PitClamp Mini.3mf]
2024-08-20 Include 3030 Modular Mount example setup photos
2024-08-20 Removing unbranded alternative files. At least for now...
    [PitClamp Mini - Base - Standard (Unbranded).step, PitClamp Mini - Base - Standard (Unbranded).stl, PitClamp Mini - Common - Upper (Unbranded).step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]
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2024-08-22 Add 57AIM ring with cable passthru
    [PitClamp Mini - Ring - iHSV57 - 5mm Offset - Cable Passthru.stl]
2024-08-28 Move Extrusion Ring to Experimental Part
    [PitClamp Mini - Printed Hinge - Clip.step, PitClamp Mini - Printed Hinge - Nut.step, PitClamp Mini - Printed Hinge - Pin.step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]
2024-08-29 Update standard to M6x18mm for 3030 extrusion
2024-08-29 Release Experimental Print-In-Place PitClamp Mini
    [PitClamp Mini - Standard - Print-In-Place.3mf, PitClamp Mini - Standard - Print-In-Place.stl]
2024-08-29 Move Extrusion Rings to Experimental
    [PitClamp Mini - Ring - Extrusion - 1mm Offset.step, PitClamp Mini - Ring - Extrusion - 6mm Offset.step]
2024-08-29 Update BOM.md
    M6x18 -> M6x15 for 3030 extrusion
2024-09-03 Fix file name for 57AIM Cable Passthru
    [PitClamp Mini - Ring - 57AIM - 5mm Offset - Cable Passthru.stl]
2024-09-03 Add ring template STEP files
    [Ring Template - 0mm Offset.step, Ring Template - 5mm Offset.step]
2024-09-04 Standard Base w/ Helper Brim Print Assist
    [PitClamp Mini - Base - Standard - Lower - With Helper Brim.step]
2024-09-05 Add OSSM Logo Template
    [OSSM Logo Template.f3d]
2024-09-09 Add new "Default" rings, BOM simplifies to (4)M5x40 for 57AIM and iHSV57 Rings when using Default OSSM Head
    [PitClamp Mini - Ring - 57AIM - Default - 5mm Offset.stl]
2024-09-09 Refactor for official v1.0 release
    [OSSM Logo Template.f3d, PitClamp Mini - Base - Folding - Lower.step, PitClamp Mini - Base - Folding - Lower.stl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]
2024-09-17 Add v1.1 Ring (Future)
    [PitClamp Mini - Ring v1.1 - 57AIM - Default - 5mm Offset.stl]
2024-09-21 Remove v1.1 ring temporarily
    [PitClamp Mini - Ring v1.1 - 57AIM - Default - 5mm Offset.stl]
2024-11-22 Latest Recommended 57AIM Ring
    [PitClamp Mini - Ring v1.1 - 57AIM - 5mm Offset +Passthru.stl]
2024-12-17 Fix non-manifold edges on Upper
    [PitClamp Mini - Common - Upper.step, PitClamp Mini.3mf]
2025-01-12 Increase tolerance to .4mm from .2mm for easier assembly
2025-01-12 .3mm Tolerance 60AIM40F Ring
2025-02-28 Rename Files/Rings/STEP/PitClamp Mini - Ring - 57AIM - Alternate - 5mm Offset.step to Files/Rings/STEP/DEPRECATED/PitClamp Mini - Ring - 57AIM - Alternate - 5mm Offset.step
    Deprecate 57AIM v1.0 Rings
    [PitClamp Mini - Ring - 57AIM - Alternate - 5mm Offset.step]
2025-02-28 Rename Files/Rings/STEP/PitClamp Mini - Ring - 57AIM - Default - 5mm Offset.step to Files/Rings/STEP/DEPRECATED/PitClamp Mini - Ring - 57AIM - Default - 5mm Offset.step
    [PitClamp Mini - Ring - 57AIM - Default - 5mm Offset.step]
2025-02-28 Deprecate v1.0 57AIM Rings
    [PitClamp Mini - Ring - 57AIM - Alternate - 5mm Offset.stl]
